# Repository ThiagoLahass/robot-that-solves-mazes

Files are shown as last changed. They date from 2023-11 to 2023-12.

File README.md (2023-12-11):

# robot-that-solves-mazes
Apply concepts acquired throughout the course such as pulse width modulation (PWM) for controlling DC motors and servomotors, analog-to-digital conversion (ADC) for data collection signals from analog sensors, port control (GPIO, General Purpose Input/Output), Timers, LCD, among others.

<div style="display: flex; justify-content: space-between;">
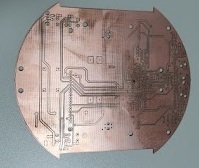
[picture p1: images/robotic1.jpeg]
  
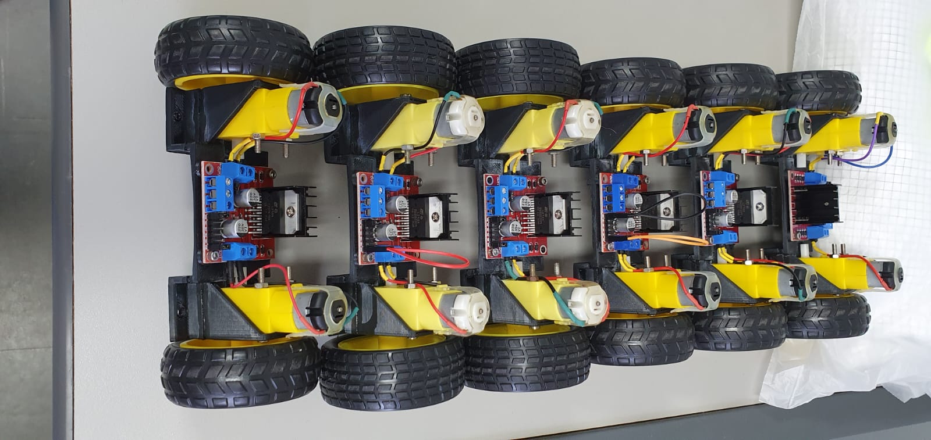
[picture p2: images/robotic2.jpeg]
  
</div>

## Video Demonstration

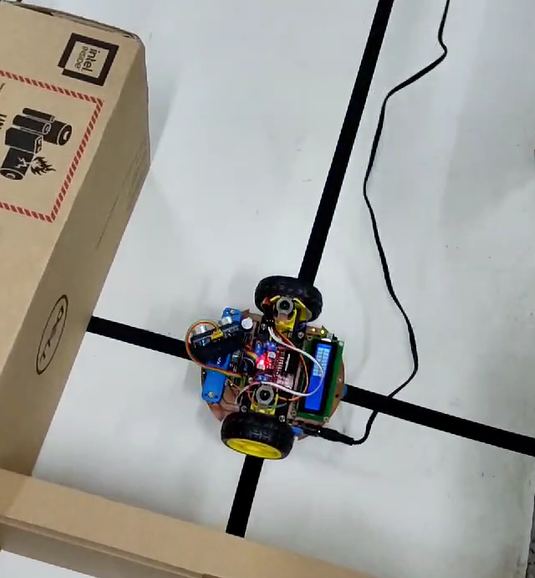
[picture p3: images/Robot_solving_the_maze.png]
Watch the Demo Video (https://youtu.be/FQmdxKDgYJk)


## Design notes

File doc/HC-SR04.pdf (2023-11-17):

## HC-SR04 Ultrasonic Sensor

### Elijah J. Morgan Nov. 16 2014

The purpose of this file is to explain how the HC-SR04 works. It will give a brief explanation of how ultrasonic sensors work in general. It will also explain how to wire the sensor up to a microcontroller and how to take/interpret readings. It will also discuss some sources of errors and bad readings.

### 1. How Ultrasonic Sensors Work 2. HC-SR04 Specifications 3. Timing chart, Pin explanations and Taking

Distance Measurements

### 4. Wiring HC-SR04 with a microcontroller 5. Errors and Bad Readings

### 1. How Ultrasonic Sensors Work

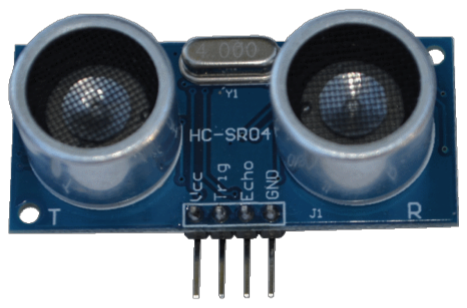
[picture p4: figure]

Ultrasonic sensors use sound to determine the distance between the sensor and the closest object in its path. How do ultrasonic sensors do this? Ultrasonic sensors are essentially sound sensors, but they operate at a frequency above human hearing.

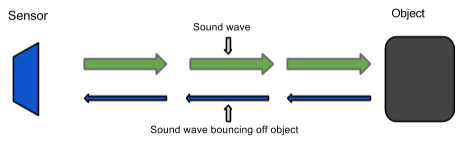
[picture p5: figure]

The sensor sends out a sound wave at a specific frequency. It then listens for that specific sound wave to bounce off of an object and come back (Figure 1). The sensor keeps track of the time between sending the sound wave and the sound wave returning. If you know how fast something is going and how long it is traveling you can find the distance traveled with equation 1.

Equation 1. d = v × t

The speed of sound can be calculated based on the a variety of atmospheric conditions, including temperature, humidity and pressure. Actually calculating the distance will be shown later on in this document.
It should be noted that ultrasonic sensors have a cone of detection, the angle of this cone varies with distance, Figure 2 show this relation. The ability of a sensor to detect an object also depends on the objects orientation to the sensor. If an object doesn’t present a flat surface to the sensor then it is possible the sound wave will bounce off the object in a way that it does not return to the sensor.

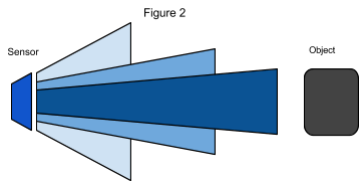
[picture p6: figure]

### 2. HC-SR04 Specifications

The sensor chosen for the Firefighting Drone Project was the HC-SR04. This section contains the specifications and why they are important to the sensor module. The sensor modules requirements are as follows.
- Cost
- Weight
- Community of hobbyists and support
- Accuracy of object detection
- Probability of working in a smoky environment
- Ease of use
The HC-SR04 Specifications are listed below. These specifications are from the Cytron Technologies HC-SR04 User’s Manual (source 1).
- Power Supply: +5V DC
- Quiescent Current: <2mA
- Working current: 15mA
- Effectual Angle: <15º
- Ranging Distance: 2-400 cm
- Resolution: 0.3 cm
- Measuring Angle: 30º
- Trigger Input Pulse width: 10uS
- Dimension: 45mm x 20mm x 15mm
- Weight: approx. 10 g

The HC-SR04’s best selling point is its price; it can be purchased at around $2 per unit.

### 3. Timing Chart and Pin Explanations

The HC-SR04 has four pins, VCC, GND, TRIG and ECHO; these pins all have different functions. The VCC and GND pins are the simplest they power the HC-SR04. These pins need to be attached to a +5 volt source and ground respectively. There is a single control pin: the TRIG pin. The TRIG pin is responsible for sending the ultrasonic burst. This pin should be set to HIGH for 10 μs, at which point the HC-SR04 will send out an eight cycle sonic burst at 40 kHZ. After a sonic burst has been sent the ECHO pin will go HIGH. The ECHO pin is the data pin it is used in taking distance measurements. After an ultrasonic burst is sent the pin will go HIGH, it will stay high until an ultrasonic burst is detected back, at which point it will go LOW.
Taking Distance Measurements
The HC-SR04 can be triggered to send out an ultrasonic burst by setting the TRIG pin to HIGH. Once the burst is sent the ECHO pin will automatically go HIGH. This pin will remain HIGH until the the burst hits the sensor again. You can calculate the distance to the object by keeping track of how long the ECHO pin stays HIGH. The time ECHO stays HIGH is the time the burst spent traveling. Using this measurement in equation 1 along with the speed of sound will yield the distance travelled. A summary of this is listed below, along with a visual representation in Figure 2.
1. Set TRIG to HIGH
2. Set a timer when ECHO goes to HIGH
3. Keep the timer running until ECHO goes to LOW
4. Save that time
5. Use equation 1 to determine the distance travelled

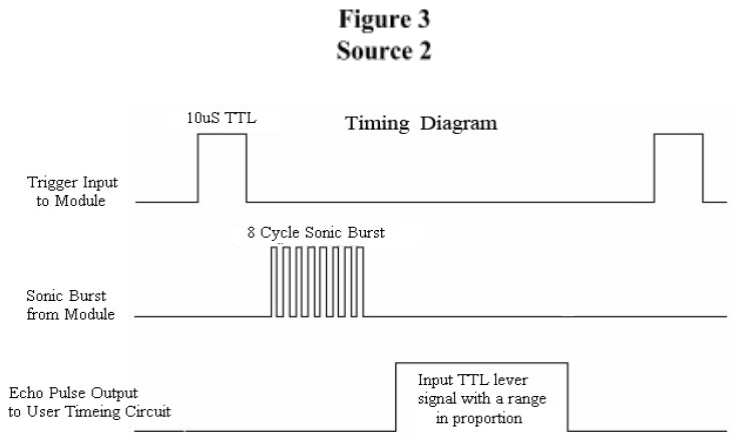
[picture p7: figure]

Source 2

To interpret the time reading into a distance you need to change equation 1. The clock on the device you are using will probably count in microseconds or smaller. To use equation 1 the speed of sound needs to determined,which is 343 meters per second at standard temperature and pressure. To convert this into more useful form use equation 2 to change from meters per second to microseconds per centimeter. Then equation 3 can be used to easily compute the distance in centimeters.

Equation 2. Distance =

Speed
170.15 m × 100 cm

Meters ×

1e6 μS
170.15 m × cm

58.772 μS

Equation 3. Distance = 58 | m

time =

μs
μs/cm = c

### 4. Wiring the HC-SR04 to a Microcontroller

This section only covers the hardware side. For information on how to integrate the software side, look at one of the links below or look into the specific microcontroller you are using.

The HC-SR04 has 4 pins: VCC, GND, TRIG and ECHO.
1. VCC is a 5v power supply. This should come from the microcontroller
2. GND is a ground pin. Attach to ground on the microcontroller.
3. TRIG should be attached to a GPIO pin that can be set to HIGH
4. ECHO is a little more difficult. The HC-SR04 outputs 5v, which could destroy many microcontroller GPIO pins (the maximum allowed voltage varies). In order to step down the voltage use a single resistor or a voltage divider circuit. Once again this depends on the specific microcontroller you are using, you will need to find out its GPIO maximum voltage and make sure you are below that.

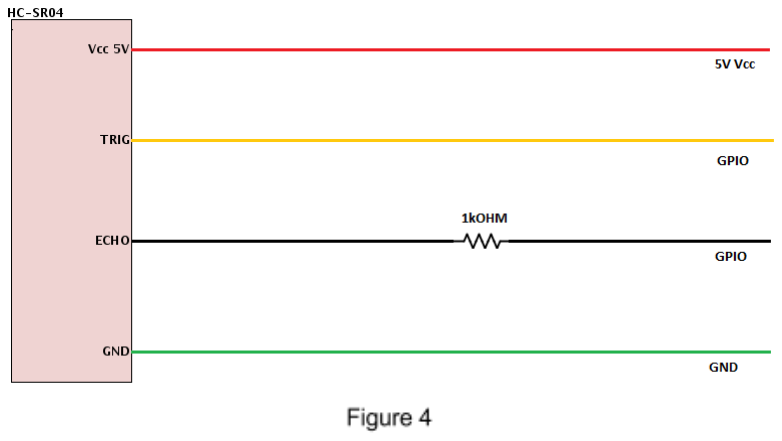
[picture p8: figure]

### 5. Errors and Bad Readings

Ultrasonic sensors are great sensors they work well for many applications where other types of sensors fall short. Unfortunately, they do have weaknesses. These weaknesses can be mitigated and worked around, but first they must be understood. The first weakness is that they use sound. There is a limit to how fast ultrasonic sensors can get distance measurements. The longer the distance, the slower they are at reporting the distance. The second weakness comes from the way sound bounces off of objects. In enclosed spaces it is possible, if not probable that there will be unintended echos. The echos can very easily cause false short readings. In Figure 2 a pulse was sent out. It bounced off of object 1 and returned to the sensor. The distance was recorded and then a new pulse was sent. There was another object farther away, so that when the new pulse reaches object 1, the first signal will reach the sensor. This will cause the sensor to think that there is an object closer than is actually true. The old pulse is smaller than the new pulse because it has grown weaker. The longer the pulse exists the weaker it grows until it is negligible. If multiple sensors are being used, the number of echos will increase along with the number of errors. There are two main ways to reduce the number of errors. The first is to provide shielding around the sensor. This prevents echos coming in from angle outside what the sensor should actually pick up. The second is to reduce the frequency at which pulses are sent out. This gives more time for the echos to dissipate.

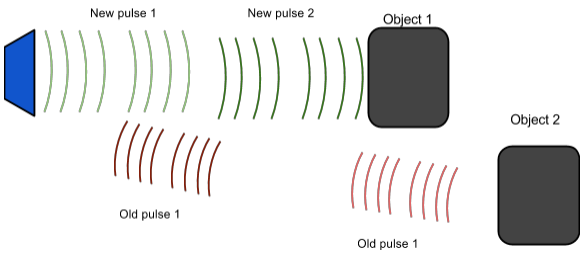
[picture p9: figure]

Works Cited

Source 1.
“HC-SR04 User's_Manual.” docs.google. Cytron Technologies, May 2013 Web. 5 Dec. 2009.
<https://docs.google.com/document/d/1Y-yZnNhMYy7rwhAgyL_pfa39RsB-x2qR4vP8saG73rE/edit>

Source 2.
“Attiny2313 Ultrasonic distance (HR-SR04) example.” CircuitDB. n.a. 7 Sept. 2014 Web. 5 Dec. 2014. <http://www.circuitdb.com/?p=1162>

Links

These are not formatted; you will need to copy and paste them into your web browser.

Want to learn about Ultrasonic Sensors in general? http://www.sensorsmag.com/sensors/acousticultrasound/choosingultrasonicsensorprox imityordistancemeasurement-825

All about the HC-SR04

- http://www.circuitdb.com/?p=1162
- http://www.micropik.com/PDF/HCSR04.pdf
- http://randomnerdtutorials.com/completeguideforultrasonicsensorhcsr04/
- http://www.ezdenki.com/ultrasonic.php
(^fantastic tutorial, explains a lot of stuff)
- http://www.elecrow.com/hcsr04-ultrasonicrangingsensorp-316.html
(^ this one has some cool charts)

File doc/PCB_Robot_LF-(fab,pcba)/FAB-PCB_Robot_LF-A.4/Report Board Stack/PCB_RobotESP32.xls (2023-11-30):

Board Stack Report
Stack Up |  | Layer Stack
Layer | Board Layer Stack | Name | Material | Thickness | Constant
1 |  | Top Paste
2 |  | Top Overlay
3 |  | Top Solder | Solder Resist | 0.40mil | 3.5
4 |  | Top Layer | Copper | 1.40mil
5 |  | Dielectric 1 | FR-4 | 12.60mil | 4.8
6 |  | Bottom Layer | Copper | 1.40mil
7 |  | Bottom Solder | Solder Resist | 0.40mil | 3.5
8 |  | Bottom Overlay
9 |  | Bottom Paste
 | Height : 16.20mil

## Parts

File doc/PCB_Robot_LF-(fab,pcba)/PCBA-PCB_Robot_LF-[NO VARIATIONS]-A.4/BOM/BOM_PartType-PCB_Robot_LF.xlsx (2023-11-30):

Comment | Description | Designator | Footprint | LibRef | Quantity
MPU-6050 | 3-axis gyroscope, 3-axis accelerometer |  | PCBComponent_1 | CMP-1172158-22 | 1
2AA-BH | holder for 2AA Batteries | B1, B2 | PCB-372er05q764edivmfsgk-1 | CMP-3614-18 | 2
2.2 nF | Cap Ceramic 0.1uF 100V X7R 10% SMD 0805 125°C Embossed Plastic T/R | C1, C2, C3, C4, C5 | PCB-uuh55xovs16kiz8jvqzd-1 | CMP-27afecb34382f868-1 | 5
Zener 5V | Zener Diode Single 5.6V | D1 | Vishay TZMB5V6-GS08-Footprint-1 | CMP-0f7fc64f132dd0b8-2 | 1
Taiwan Semiconductor SS14L | Diode: Schottky rectifying; 40V; 1A; subSMA | D2, D5 | SS14L | CMP-32c6fbb69da8ed01-1 | 2
Bivar SM0805GCL | LED; SMD; 0805; Green; 575nm; 3.6mcd; Water Clr Lens; 130Deg Viewing Angle; Low Current | D3, D4 | PCB-iso4q9antg7ukfc6uypa-1 | CMP-5ccb9491e398830c-1 | 2
Custom LCD | Custom LCD | DS* | PCB-a1k1vgfry79p3zq61c6u-1 | CMP-bd58754c3093629f-2 | 1
Molex 10-89-7061 | Conn.; Rect./PCB; Breakaway Header; 6 Cir.; 2-Row; Vert.; C-Grid Series; High Temp; Tin | J1, J2, J3, J4, J5 | PCB-cmxxrm6j1415z55ls37o-1 | CMP-a3b96ab7ba957c7e-1 | 5
Würth Elektronik 694108301002 | DC Power Jack Connector WR-DC, Male, Right Angled, THT, 5 A, 24 V | J6 | PCB-vi56m6hkignhj9lwk7ra-1 | CMP-fe0834211d6821cf-4 | 1
GPS NEO-6M | KK 254 Solid Header, Vertical, with Friction Lock, 4 Circuits, Tin (Sn) Plating | J7 | PCB-hddxo6oxno0y1grizy36-1 | CMP-cef707fdef991130-9 | 1
HC-S04 | KK 254 Solid Header, Vertical, with Friction Lock, 4 Circuits, Tin (Sn) Plating | J8 | PCB-hddxo6oxno0y1grizy36-1 | CMP-cef707fdef991130-9 | 1
MotoresDC | Conn Unshrouded Header HDR 8 POS 2.54mm Solder ST Top Entry Thru-Hole Bag/Box | JP1 | PCB-zdm29xznpx2fif9lk3na-1 | CMP-1d33d663ca37c2f4-5 | 1
150080YS75000 | SMD mono-color Chip LED; WL-SMCW; Yellow | LED1, LED2 | 0805_A | CMP-12518870-5 | 2
MP2307_Buck | MP2307 Buck | Module1 | PCB-8fho96w7wpsiqoq4hq4v-1 | CMP-f3b73942b0d12c70-1 | 1
ServoMotor | AMPMODU 3 Position Through-Hole Single Row 0.1 Inch Straight Breakaway Header | P1 | PCB-t3j82fujp56a0y7cbkwq-1 | CMP-56249debc17089e3-37 | 1
TRCT5000_3 | Optical Switches, Reflective, Phototransistor Output 12mm Sense 950nm | Q1 | PCB-TCRT5000 | CMP-udi2hivl2amq5tnk7plz-1 | 1
TRCT5000 | Optical Switches, Reflective, Phototransistor Output 12mm Sense 950nm | Q2, Q3, Q4, Q5 | PCB-TCRT5000 | CMP-udi2hivl2amq5tnk7plz-1 | 4
MMBTH10LT1G | VHF / UHF Transistor, NPN Silicon, 3-Pin SOT-23, Pb-Free, Tape and Reel | Q6, Q7, Q8, Q9, Q10 | ONSC-SOT-23-3-318-08_V | CMP-851888-2 | 5
220 | Res Thick Film 0805 330 Ohm 1% 1/8W ±100ppm/°C Molded SMD SMD | R1, R2, R19, R20, R21, R22, R23 | CAPC2013X94X50ML20T25 | CMP-d14418bba6eb0e83-1 | 7
330 | Res Thick Film 0805 330 Ohm 1% 1/8W ±100ppm/°C Molded SMD SMD | R3, R4, R5, R6, R7, R8, R9, R10, R11, R18, R24, R25 | CAPC2013X94X50ML20T25 | CMP-d14418bba6eb0e83-1 | 12
1 k | Res Thick Film 0805 330 Ohm 1% 1/8W ±100ppm/°C Molded SMD SMD | R12, R13, R14, R15, R26, R27, R28, R29, R30, R33 | CAPC2013X94X50ML20T25 | CMP-d14418bba6eb0e83-1 | 10
4k7 | Res Thick Film 0805 330 Ohm 1% 1/8W ±100ppm/°C Molded SMD SMD | R16 | CAPC2013X94X50ML20T25 | CMP-d14418bba6eb0e83-1 | 1
3k7 | Res Thick Film 0805 330 Ohm 1% 1/8W ±100ppm/°C Molded SMD SMD | R17 | CAPC2013X94X50ML20T25 | CMP-d14418bba6eb0e83-1 | 1
2 k | Res Thick Film 0805 330 Ohm 1% 1/8W ±100ppm/°C Molded SMD SMD | R31 | CAPC2013X94X50ML20T25 | CMP-d14418bba6eb0e83-1 | 1
47 k | Res Thick Film 0805 330 Ohm 1% 1/8W ±100ppm/°C Molded SMD SMD | R32 | CAPC2013X94X50ML20T25 | CMP-d14418bba6eb0e83-1 | 1
SPI | Conn Unshrouded Header HDR 6 POS 2.54mm Solder ST Thru-Hole - No Outline | SPI | PCB-2xrknp0frdgvb29ud8aa-1 | CMP-88ed4362af17572a-9 | 1
C&K Components OS102011MA1QS1 | Switch Slide ON ON SPDT Side Slide 0.1A 12VDC 10000Cycle PC Pins Bracket Mount/Through Hole Bulk | SW1 | PCB-a78kgj8v3nza1899t3lg-1 | CMP-85734c5fa66e5ab4-3 | 1
TE Connectivity 1825910-6 | Switch Push Button OFF (ON) SPST Round Button 0.05A 24VDC Momentary Contact PC Pins Thru-Hole | SW2, SW3, SW4, SW5 | PCB-s0s7ww4bjhs8rpuf9xpk-1 | CMP-49fa8280b69c963d-7 | 4
MT3608 Module | MT3608 Module DC - DC Boost | U | MT3608-Module | CMP-da4e14b3e5cd0589-10 | 1
ESP32 Custom | Eval Board For ESP-WROOM-32 - 38pin module with 8.4mm header | U2 | PCB-v7o6mlcnvy9ltvisia1k-2 | CMP-0991c5192c5ed656-43 | 1
Trimmer 1/2W | Res Cermet Trimmer 2K Ohm 10% 1/2W 25(Elec)Turn 2.19mm (9.53 X 4.83 X 11.55mm) Pin Thru-Hole Tube | VR1 | PCB-5abvnr99iwiiosfurk6j-1 | CMP-a8df61d7bf077718-3 | 1
OBO 1206A | Audio Buzzer Piezo 85dB | X1 | PCB-o5yglm5fvhcnnvl903n6-1 | CMP-hk97o7c7kcbk1p7rfoz4-1 | 1

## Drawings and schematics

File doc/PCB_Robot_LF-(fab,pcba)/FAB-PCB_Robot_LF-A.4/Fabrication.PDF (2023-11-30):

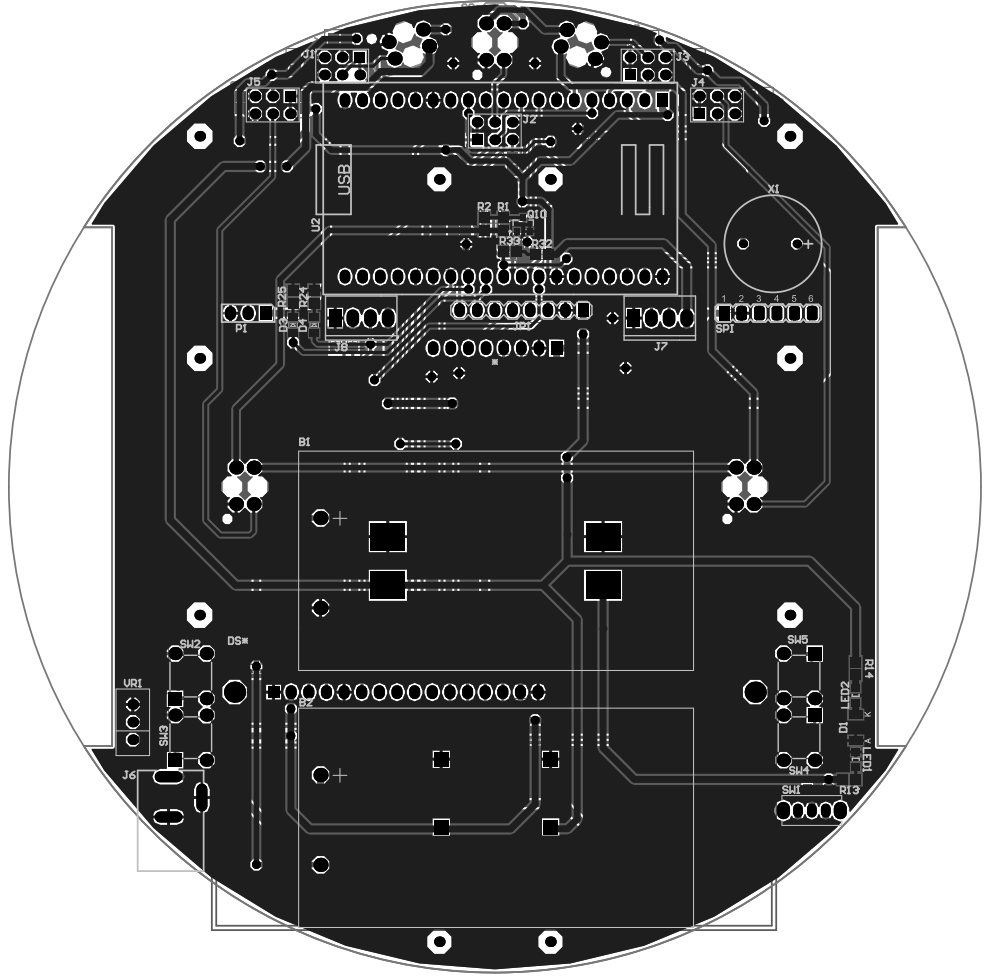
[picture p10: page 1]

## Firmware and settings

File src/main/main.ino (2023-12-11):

#include <ESP32Servo.h>
#include "Wire.h"
#include <MPU6050_light.h>
#include <string.h>

#define     HIGH        1
#define     LOW         0

//=== NAMING THE PORTS ===
#define     SLC         32
#define     SR          39
#define     SC          34
#define     SL          35
#define     SRC         36
#define     E_CH1       33
#define     CHA_M1      25
#define     E_CH2       26
#define     CHA_M2      27
#define     BUZZER      14
#define     BL_LCD      12
#define     SERVO       13
#define     DB4         15
#define     DB5         2
#define     DB6         0
#define     DB7         4
#define     EN_TRIG     16
#define     RS          17
#define     CS_SENSORS  5
#define     CLK         18
#define     MISO_ECHO   19
#define     SDA_MPU     21
#define     RX0         3
#define     TX0         1
#define     SCL_MPU     22
#define     MOSI        23
//=========================

//============================= LCD COMMANDS =============================
const int DATA[] = {4, 0, 2, 15};
#define     DATA_SIZE 4

// Commands: [- - - RS D7 D6 D5 D4]
#define     FUNCTION_SET 	      0x20 	// 0010 0000 - 4 bits
#define     DISPLAY_CONTROL     0x0C 	// 0000 1100
#define     CLEAR_DISPLAY 	    0x01 	// 0000 0001
#define     RETURN_HOME 	      0x02 	// 0000 0010
#define     ENTRY_MODE_SET 	    0x06 	// 0000 0110

// States
#define     LCD_DISPLAYON 		  0x04
#define     LCD_DISPLAYOFF 		  0x00
#define     DISPLAY_FUNCTION 	  0x08
#define     ENTER 				      0xA8  //1010 1000
#define     DISPLAY_SHIFT_LEFT 	0x18  //0001 1000
#define     DISPLAY_SHIFT_RIGHT 0x1C  //0001 1100

void pulseEnable();
void initLCD();
void write4bits(int value);
void write8bits(int value);

void writeData(const char* value){
  char c;
  for (int i = 0; i < strlen(value); i++){
    c = value[i];
    
    digitalWrite(RS, HIGH);
    write8bits(c);
    digitalWrite(RS, LOW);
  }
}

void display_sensors_values_on_LCD();
// ============================= END LCD COMMANDS =============================

// Private Objects and Variables for giroscope
MPU6050 mpu(Wire);
unsigned long timer = 0;

// DEFINES OF VALUES RELATED TO ENGINE CONTROL
#define     PWM1_Ch     2       // Direita
#define     PWM2_Ch     3       // Esquerda
#define     PWM_Res     8
#define     PWM_Freq    1000

#define     LINE_THRESHOLD_VALUE 500      // line reading cut-off value
#define     WALL_THRESHOLD_VALUE 30       // wall reading cut-off value
#define     ANGLE_TURN_VALUE 83           // angle that robot must turn based on giroscope value
#define     TIME_TO_RESTART 15            // seconds
#define     NUM_SENSORS 5

unsigned int sensors[NUM_SENSORS]       = {0};      // an array to hold sensor values
unsigned int sensors_max[NUM_SENSORS]   = {0};      // used to calibrate the initial values of the IR sensors
unsigned int sensors_min[NUM_SENSORS]   = {4096};   // used to calibrate the initial values of the IR sensors

float Kp = 0.008, Ki = 0, Kd = 0;                   // values of the PID constants values

char path[100] = "";

unsigned char path_length = 0;                      // the length of the path


float moving_average(float *buffer, int tamanho);

float read_ultrasonic_sensor();

void follow_segment();

void turn_off_motors();

void read_line();

void turn(char dir);

char select_turn(unsigned char found_left, unsigned char found_straight, unsigned char found_right);

void simplify_path();

void set_motors(int right_motor, int left_motor);

void lcd_load_custom_character();

const int SIZE_MOVING_AVERAGE = 5;
float buffer[SIZE_MOVING_AVERAGE] = {0};

Servo servo;                        // create servo object to control a servo
int pos = 0;                        // variable to store the servo position

float average_distance = 0;         // average distance read by the ultrasonic sensor

void setup() {
  Serial.begin(115200);
  Wire.begin();
  byte status = mpu.begin();
  while(status != 0){ }             // stop everything if could not connect to MPU6050
  delay(500);
  mpu.calcOffsets();                // gyro and accelero

  pinMode(EN_TRIG, OUTPUT);
  pinMode(MISO_ECHO, INPUT);

  pinMode(BUZZER, OUTPUT);
  digitalWrite(BUZZER, LOW);

  servo.attach(SERVO, 500, 2500);   // attaches the servo on pin SERVO to the servo object
  servo.write(90);                  // Position the servo in the central position
  delay(500);

  pinMode(SLC       , INPUT);
  pinMode(SR        , INPUT);
  pinMode(SC        , INPUT);
  pinMode(SL        , INPUT); 
  pinMode(SRC       , INPUT);
  pinMode(CS_SENSORS, OUTPUT);

  digitalWrite(CS_SENSORS, HIGH);

  pinMode(E_CH1, OUTPUT);
  pinMode(E_CH2, OUTPUT);

  ledcAttachPin(CHA_M1, PWM1_Ch);
  ledcSetup(PWM1_Ch, PWM_Freq, PWM_Res);

  ledcAttachPin(CHA_M2, PWM2_Ch);
  ledcSetup(PWM2_Ch, PWM_Freq, PWM_Res);

  // ========================== LCD ==========================
  pinMode(RS, OUTPUT);
  pinMode(EN_TRIG, OUTPUT);
  
  for (int i = 0; i < DATA_SIZE; i++){
    pinMode(DATA[i], OUTPUT);
  }

  initLCD();
  
  // Always good to clear and return home
  write8bits(CLEAR_DISPLAY);
  write8bits(RETURN_HOME);
  delay(2);                         // 1.52ms delay needed for the Return Home command

  writeData("Thiago Lahass");
  write8bits(ENTER);
  writeData("Eng Computacao");
}
    
void loop() {
  //======================== APPLYING LEARNING ALGORITHM ========================
  while(1){
    delay(100);

    follow_segment();

    read_line();
    // If we no longer find a visible line, we finish the maze and can restart from the optimized path
    if(sensors[1] < LINE_THRESHOLD_VALUE && sensors[2] < LINE_THRESHOLD_VALUE && sensors[3] < LINE_THRESHOLD_VALUE ){
      Serial.println("No lines found, DONE!!!");
      break;
    }

    // set the motors bit more slowly
    set_motors(158, 94); // (128 + 30, 128 - 34) - apparently the motor on the right runs a little more with the same pwm than the one on the left, hence the difference
    read_line();

    // If the crossing sensors are already on the line, leave immediately
    // if not, walk a little further until you find the crossing line.
    while(sensors[0] < LINE_THRESHOLD_VALUE && sensors[4] < LINE_THRESHOLD_VALUE){
      read_line();
    }

    // stop the motors
    turn_off_motors();
    delay(100);

    //================== FOLLOWING THE MAZE ACCORDING TO THE WALLS ==================
    //================================ READ THE WALLS ===============================
    unsigned char found_left      = 0;
    unsigned char found_straight  = 0;
    unsigned char found_right     = 0;

    servo.write(90);                                    // Servo facing forward
    delay(500);
    average_distance = read_ultrasonic_sensor();
    display_sensors_values_on_LCD();
    
    if(average_distance > WALL_THRESHOLD_VALUE){
      found_straight = 1;
      Serial.println("found_straight");
    }

    servo.write(180);                                   // Servo facing left
    delay(500);
    average_distance = read_ultrasonic_sensor();
    display_sensors_values_on_LCD();

    if( average_distance > WALL_THRESHOLD_VALUE ){      // If the left is free, we can take it immediately
      found_left = 1;
      Serial.println("found_left");
    } 
    else{
      servo.write(0);                                   // Servo facing right
      delay(500);
      average_distance = read_ultrasonic_sensor();
      display_sensors_values_on_LCD();

      if(average_distance > WALL_THRESHOLD_VALUE){
        found_right = 1;
        Serial.println("found_right");
      }
    }

    servo.write(90);                                    // Servo facing forward
    //============================ END OF THE READ WALLS SECTION ==============================

    // Intersection identification is complete.

    unsigned char dir = select_turn(found_left, found_straight, found_right);
    Serial.print("Direção: ");
    Serial.println((char)dir);
    
    // Make the turn indicated by the path.
    turn(dir);
    
    // Store the intersection in the path variable.
    path[path_length] = dir;
    path_length ++;

    Serial.print("Path: ");
    Serial.println(path);

    // simplify the path
    simplify_path();
    Serial.print("Simplified Path: ");
    Serial.println(path);
  }
  
  // Now enter an infinite loop - we can re-run the maze as many times as we want to.
  while(1) {
    // Always good to clear and return home
    write8bits(CLEAR_DISPLAY);
    write8bits(RETURN_HOME);
    delay(2);                               // 1.52ms delay needed for the Return Home command

    writeData("DONE!!!");
    write8bits(ENTER);
    writeData("Restart please...");
    delay(1000);

    
    // Always good to clear and return home
    write8bits(CLEAR_DISPLAY);
    write8bits(RETURN_HOME);
    delay(2);                               // 1.52ms delay needed for the Return Home command
    writeData("Restarting in...");
    
    int j = 0;
    for(j = 0; j < TIME_TO_RESTART; j++) {
      
      char line[25];
      line[0] = '\0';
      dtostrf(j, 6, 2, line);
      strcat(line, " s");

      // writeData("Restarting in...");
      write8bits(ENTER);
      writeData(line);
      delay(1000);
    }

    int i;
    for(i = 0; i < path_length; i++) {
      // SECOND MAIN LOOP BODY
      follow_segment();
      
      // Drive straight while slowing down, as before.
      set_motors(158, 94);  // (128 + 30, 128 - 34) - apparently the motor on the right runs a little more with the same pwm than the one on the left, hence the difference
      read_line();

      // If the crossing sensors are already on the line, leave immediately
      // if not, walk a little further until you find the crossing line.
      while(sensors[0] < LINE_THRESHOLD_VALUE && sensors[4] < LINE_THRESHOLD_VALUE){
        read_line();
      }

      // stop the motors
      turn_off_motors();
      delay(100);
    
      // Make a turn according to the instruction stored in
      // path[i].
      turn(path[i]);
    }
    // Follow the last segment up to the finish.
    follow_segment();
    
    // Now we should be at the finish! Restart the loop.
  }
}

// Function to calculate the moving average
float moving_average(float *buffer, int size) {
    float sum = 0.0;
    for (int i = 0; i < size; ++i) {
        sum += buffer[i];
    }
    return sum / size;
}

// Function to obtain reading from the ultrasonic sensor
float read_ultrasonic_sensor() {
    float duration, distance;
    for(int i = 0; i < SIZE_MOVING_AVERAGE; i++){
        // Send a short pulse to the Trig pin to activate measurement
        digitalWrite(EN_TRIG, LOW);
        delayMicroseconds(10);
        digitalWrite(EN_TRIG, HIGH);
        delayMicroseconds(10);
        digitalWrite(EN_TRIG, LOW);

        // Measure pulse duration on Echo pin
        duration = pulseIn(MISO_ECHO, HIGH);

        // Convert duration to distance (considering speed of sound ~343m/s)
        distance = duration * 0.0343 / 2;

        buffer[i] = distance;
    }

    // Calculation of the moving average
    float average_distance = moving_average(buffer, SIZE_MOVING_AVERAGE);

    return average_distance;
}


// FOLLOWING A SEGMENT USING ON-OFF CONTROL (not used here, for testing only)
void follow_segment_on_off() {
    while(1) {
        read_line();

        if( sensors[1] > LINE_THRESHOLD_VALUE ){        // must rotate to right
          set_motors(128+42, 128-22);
        }
        else if( sensors[3] > LINE_THRESHOLD_VALUE ){   // must rotate to left
          set_motors(128+22, 128-42);
        }
        else if( sensors[2] > LINE_THRESHOLD_VALUE  ){
          set_motors(128+42, 128-42);
        }
        else{
          set_motors(128, 128);
        }
    }
}


// FOLLOWING A SEGMENT USING PID CONTROL
void follow_segment() {
    int     last_proportional_left   = 0;
    long    integral_left            = 0;

    int     last_proportional_right  = 0;
    long    integral_right           = 0;

    unsigned long initial_time, atual_time;
    initial_time = millis();

    while(1) {
        read_line();

        // The "proportional" term should be 0 when we are on the line.
        float proportional_left  = sensors[1];
        float proportional_right = sensors[3];

        // Compute the left derivative (change) and integral (sum) of the position.
        int derivative_left = proportional_left - last_proportional_left;
        integral_left += proportional_left;

        // Compute the right derivative (change) and integral (sum) of the position.
        int derivative_right = proportional_right - last_proportional_right;
        integral_right += proportional_right;

        // Remember the last position.
        last_proportional_left = proportional_left;
        last_proportional_right = proportional_right;

        // Compute the difference between the two motor power settings,
        // m1 - m2. If this is a positive number the robot will turn
        // to the left. If it is a negative number, the robot will
        // turn to the right, and the magnitude of the number determines
        // the sharpness of the turn.
        int power_difference_left  = proportional_left*Kp + integral_left*Ki + derivative_left*Kd;
        int power_difference_right = proportional_right*Kp + integral_right*Ki + derivative_right*Kd;

        set_motors(167 + power_difference_left, 85 - power_difference_right); // direita, esquerda

        // We use the inner three sensors (1, 2, and 3) for
        // determining whether there is a line straight ahead, and the
        // sensors 0 and 4 for detecting lines going to the left and
        // right.
        atual_time = millis();

        if( atual_time > initial_time + 1000){
            if(sensors[1] > LINE_THRESHOLD_VALUE && sensors[2] > LINE_THRESHOLD_VALUE && sensors[3] > LINE_THRESHOLD_VALUE ) {
              // There is no line visible ahead, and we didn't see any
              // intersection. Must be a dead end.
              Serial.println("Intersection 3 lines found");
              return;
            }
            else if(sensors[0] > LINE_THRESHOLD_VALUE || sensors[4] > LINE_THRESHOLD_VALUE){
                // Found an intersection.
                if( sensors[0] > LINE_THRESHOLD_VALUE ){
                    Serial.println("Intersection left found");
                }
                if( sensors[0] > LINE_THRESHOLD_VALUE ){
                    Serial.println("Intersection right found");
                }
                return;
            }
            else if(sensors[1] < LINE_THRESHOLD_VALUE && sensors[2] < LINE_THRESHOLD_VALUE && sensors[3] < LINE_THRESHOLD_VALUE ){
              Serial.println("No lines found, DONE!!!");
              turn_off_motors();
              return;
            }
        }
    }
}


void set_motors(int right_motor, int left_motor){
    digitalWrite(E_CH1, HIGH);
    digitalWrite(E_CH2, HIGH);
    ledcWrite(PWM1_Ch, right_motor);  // Right motor channel CHA_M1
    ledcWrite(PWM2_Ch, left_motor);   // Left  motor channel CHA_M2
    return;
}

void turn_off_motors(){
    digitalWrite(E_CH1, LOW);
    digitalWrite(E_CH2, LOW);
    return;
}

// Turns according to the parameter dir, which should be 'L', 'R', 'S' (straight), or 'B' (back).
void turn (char dir) {
  mpu.update();
  float initial_position = mpu.getAngleZ();
  float current_position = initial_position;

  Serial.print("initial_position: ");
  Serial.println(initial_position);

    switch(dir) {
        case 'L':
            // Turn left with giroscope
            Serial.println("Esquerda");
            set_motors(128+45, 128+45);
            while( current_position < initial_position + ANGLE_TURN_VALUE ){
              mpu.update();
              current_position = mpu.getAngleZ();
              // Serial.println(current_position);
            }

            turn_off_motors();
            break;

            // Turn left with infra-red line sensors
            // set_motors(128+35, 128+35);
            // Serial.println(mpu.getAngleZ());
            // while( sensors[2] > LINE_THRESHOLD_VALUE ){
            //   read_line();
            // }
            // while(sensors[2] < LINE_THRESHOLD_VALUE){
            //   read_line();
            // }
            // set_motors(128, 128);
            // break;

        case 'R':
            // Turn right with giroscope
            Serial.println("Direita");
            set_motors(128-45, 128-45);
            while( current_position > initial_position - ANGLE_TURN_VALUE ){
              mpu.update();
              current_position = mpu.getAngleZ();
              Serial.print("current_position: ");
              Serial.println(current_position);
            }

            turn_off_motors();
            break;

            // // Turn right with line sensors
            // set_motors(128-35, 128-35);
            // while( sensors[2] > LINE_THRESHOLD_VALUE ){
            //   read_line();
            // }
            // while(sensors[2] < LINE_THRESHOLD_VALUE){
            //   read_line();
            // }
            // set_motors(128, 128);
            // break;
        case 'B':
          // Turn around with giroscope
            Serial.println("Back");
            set_motors(128+45, 128+45);
            while( current_position < initial_position + 2 * ANGLE_TURN_VALUE + 5 ){
              mpu.update();
              current_position = mpu.getAngleZ();
              // Serial.println(current_position);
            }

            turn_off_motors();
            break;

            // // Turn around.
            // set_motors(128+35, 128+35);
            // while( sensors[2] > LINE_THRESHOLD_VALUE ){
            //   read_line();
            // }
            // while(sensors[2] < LINE_THRESHOLD_VALUE){
            //   read_line();
            // }
            // set_motors(128, 128);
            // break;
        case 'S':
            // Don't do anything!
            Serial.println("Straight");
            break;
    }
}

// ================= "left hand on the wall" strategy =================
// This function decides which way to turn during the learning phase of
// maze solving. It uses the variables found_left, found_straight, and
// found_right, which indicate whether there is an exit in each of the
// three directions, applying the "left hand on the wall" strategy.
char select_turn(unsigned char found_left, unsigned char found_straight, unsigned char found_right) {
    // Make a decision about how to turn. The following code
    // implements a left-hand-on-the-wall strategy, where we always
    // turn as far to the left as possible.
    if      (found_left)        return 'L';
    else if (found_straight)    return 'S';
    else if (found_right)       return 'R';
    else                        return 'B';
}


// Path simplification. The strategy is that whenever we encounter a
// sequence xBx, we can simplify it by cutting out the dead end. For
// example, LBL -> S, because a single S bypasses the dead end
// represented by LBL.
void simplify_path() {
    // only simplify the path if the second-to-last turn was a 'B'
    if(path_length < 3 || path[path_length-2] != 'B') return;
    
    int total_angle = 0;
    int i;
    
    for( i = 1; i <= 3; i++) {
        switch( path[path_length - i] ) {
            case 'R':
                total_angle += 90;
                break;
            case 'L':
                total_angle += 270;
                break;
            case 'B':
                total_angle += 180;
                break;
        }
    }

    // Get the angle as a number between 0 and 360 degrees.
    total_angle = total_angle % 360;

    // Replace all of those turns with a single one.
    switch(total_angle) {
        case 0:
            path[path_length - 3] = 'S';
            break;
        case 90:
            path[path_length - 3] = 'R';
            break;
        case 180:
            path[path_length - 3] = 'B';
            break;
        case 270:
            path[path_length - 3] = 'L';
            break;
    }

    // The path is now two steps shorter.
    path_length -= 2;
}


// This takes a sensor reading and returns an estimate of
// the robot’s position with respect to the line, as a number between 0 and 4000. A value of
// 0 means that the line is to the left of sensor 0, value of 1000 means that the line is directly
// under sensor 1, 2000 means that the line is directly under sensor 2, and so on.

// Here is a simplified version of the code that reads the sensors

// Through experiments, the values vary between:
// 100% WHITE =~ 0
// 100% BLACK =~ 2700
void read_line(){
  sensors[0] = analogRead(SLC);
  sensors[1] = analogRead(SL);
  sensors[2] = analogRead(SC);
  sensors[3] = analogRead(SR);
  sensors[4] = analogRead(SRC);

  // Serial.print(sensors[0]);
  // Serial.print(" ");

  // Serial.print(sensors[1]);
  // Serial.print(" ");

  // Serial.print(sensors[2]);
  // Serial.print(" ");

  // Serial.print(sensors[3]);
  // Serial.print(" ");

  // Serial.println(sensors[4]);
}

// ============================= LCD COMMANDS =============================
/* ------------------------------------------------------
	Pulses the Enable pin to send data to the display
*/
void pulseEnable(){
  // Making sure the pin is LOW at first
  digitalWrite(EN_TRIG, LOW);
  delayMicroseconds(1);
  
  // Pulse the Enable pin
  digitalWrite(EN_TRIG, HIGH);
  delayMicroseconds(1);
  digitalWrite(EN_TRIG, LOW);
  delayMicroseconds(100);
}
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

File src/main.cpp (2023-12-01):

#include <Servo.h>

#define HIGH 1
#define LOW  0

#define NUM_SENSORS 5

//=== NOMEANDO AS PORTAS ===
//#define   VCC_3_3     1
//#define   EN          2
#define     SLC         36
#define     SR          39
#define     SC          34
#define     SL          35
#define     SRC         32
#define     E_CH1       33
#define     CHA_M1      25
#define     E_CH2       26
#define     CHA_M2      27
#define     BUZZER      14
#define     BL_LCD      12
//#define   GND         14
#define     SERVO       13
//#define   SD2         16
//#define   SD3         17
//#define   CMD         18
//#define   VCC_5       19
//#define   CLK         20
//#define   SD0         21
//#define   SD1         22
#define     DB4         15
#define     DB5         2
#define     DB6         0
#define     DB7         4
#define     EN_TRIG     16
#define     RS          17
#define     CS_SENSORS  5
#define     CLK         18
#define     MISO_ECHO   19
//#define   GND         32
#define     SDA_MPU     21
#define     RX0         3
#define     TX0         1
#define     SCL_MPU     22
#define     MOSI        23
//#define   GND         38
//=========================

#define PWM1_Ch    0
#define PWM2_Ch    1
#define PWM1_Res   8
#define PWM1_Freq  1000



// The set_motors() function in the Pololu AVR Library (see Section 6 for more information) lets you
// set the duty cycle, and it uses 8-bit precision: a value of 255 corresponds to 100% duty cycle. For
// example, to get 67% on M1 and 33% on M2, you would call

// set_motors(171,84);

// To get a slowly decreasing PWM sequence like the one shown in the graph, you would need to write
// a loop that gradually decreases the motor speed over time.


unsigned int sensors[NUM_SENSORS]       = {0};      // an array to hold sensor values
unsigned int sensors_max[NUM_SENSORS]   = {1023};   // used to calibrate the initial values of the IR sensors
unsigned int sensors_min[NUM_SENSORS]   = {0};      // used to calibrate the initial values of the IR sensors

float Kp = 1/20, Ki = 0, Kd = 3/2; // values of the PID constants values


char path[100] = "";

unsigned char path_length = 0; // the length of the path


float mediaMovel(float *buffer, int tamanho);

float lerSensorUltrasonico();

void follow_segment();

void read_line();

void turn (char dir);

char select_turn(unsigned char found_left, unsigned char found_straight, unsigned char found_right);

void simplify_path();

// os valores de right_motor e left_motor devem ser os valores de duty-cycles deles
// exemplos:
// max velocidade: (100, 100)
// parado: (50, 50)
void set_motors(int right_motor, int left_motor);

unsigned int read_battery_millivolts();

void calibrate_line_sensors();

void mapping_sensors_values_to_calibrated_values();

void initialize();

void lcd_load_custom_character();

void print_character();

bool button_is_pressed();

void display_path();



const int TAMANHO_MEDIA_MOVEL = 5;
float buffer[TAMANHO_MEDIA_MOVEL] = {0};

int posicao_servo = 0;	
int direcao_atual = 0;	// 0 indica anti-horario
const int VEL_SERVO = 15; 
Servo servo;

void setup() {
    Serial.begin(9600);
    // pinMode(EN_TRIG, OUTPUT);
    // pinMode(MISO_ECHO, INPUT);

    // servo.attach(SERVO, 500, 2500);
  	// // posiciona o servo na posicao central
    // while( posicao_servo < 90 ){
    //   posicao_servo += VEL_SERVO;
    //   servo.write(posicao_servo);
    //   delay(100);
    // }

    pinMode(SLC   , INPUT);
    pinMode(SR    , INPUT);
    pinMode(SC    , INPUT);
    pinMode(SL    , INPUT); 
    pinMode(SRC   , INPUT);
    pinMode(CS_SENSORS, OUTPUT);

    digitalWrite(CS_SENSORS, HIGH);

    pinMode(E_CH1, OUTPUT);
    pinMode(E_CH2, OUTPUT);
    digitalWrite(E_CH1, HIGH);
    digitalWrite(E_CH2, HIGH);

    ledcAttachPin(CHA_M1, PWM1_Ch);
    ledcSetup(PWM1_Ch, PWM1_Freq, PWM1_Res);

    ledcAttachPin(CHA_M2, PWM2_Ch);
    ledcSetup(PWM2_Ch, PWM1_Freq, PWM1_Res);
}
    
void loop() {

  follow_segment();


    // //============ LEITURA E ATUALIZAÇÃO DA DISTANCIA DO ULTRASOM ==============
    // // Leitura do sensor ultrassônico
    // // Atualização do buffer para média móvel
    // for (int i = TAMANHO_MEDIA_MOVEL - 1; i > 0; --i) {
    //   buffer[i] = buffer[i - 1];
    // }
    // buffer[0] = lerSensorUltrasonico();

    // // Cálculo da média móvel
    // float media = mediaMovel(buffer, TAMANHO_MEDIA_MOVEL);

    // // Impressão da distância
    // Serial.print("Distancia: ");
    // Serial.println(media);

    // //========== FIM LEITURA E ATUALIZAÇÃO DA DISTANCIA DO ULTRASOM ============


    // //========== UPDATE POSICAO SERVO ==========
    // // anti-horario
    // if( direcao_atual == 0 ){
    //   if(posicao_servo >= 180){
    //       direcao_atual = 1;
    //   }
    //   else{
    //       posicao_servo += VEL_SERVO; 
    //   }
    // }
    // else{ //horario
    //   if(posicao_servo <= 0){
    //       direcao_atual = 0;
    //   }
    //   else{
    //       posicao_servo -= VEL_SERVO; 
    //   }
    // }
  
  	// servo.write(posicao_servo);
  
  	// // Impressão da posicao
    // Serial.print("Posicao: ");
    // Serial.println(posicao_servo);

    // //========== FIM UPDATE POSICAO SERVO ==========


    // // read the sensor:
    // read_line();
    // //calibrate the values
    // calibrate_line_sensors();

    // // AQUI TEMOS OS VALORES JÁ CALIBRADOS


    // delay(100);  // Aguarda 0.1 segundo        

    // while(1) {
    //     // FIRST MAIN LOOP BODY
    //     // (when we find the goal, we use break; to get out of this)
        
    //     follow_segment();
        
    //     // Drive straight a bit. This helps us in case we entered the intersection at an angle.
    //     // Note that we are slowing down - this prevents the robot from tipping forward too much.
    //     set_motors(50,50);
    //     delay(50);

    //     // These variables record whether the robot has seen a line to the
    //     // left, straight ahead, and right, whil examining the current intersection.
    //     unsigned char found_left        = 0;
    //     unsigned char found_straight    = 0;
    //     unsigned char found_right       = 0;

    //     unsigned int sensors[5];

    //     // Now read the sensors and check the intersection type.        
    //     read_line(sensors);

    //     // Check for left and right exits.
    //     if(sensors[0] > 100) found_left  = 1;
    //     if(sensors[4] > 100) found_right = 1;

    //     // Drive straight a bit more - this is enough to line up our wheels with the intersection.
    //     set_motors(40,40);
    //     delay(200);

    //     // Check for a straight exit.
    //     read_line(sensors);

    //     if(sensors[1] > 200 || sensors[2] > 200 || sensors[3] > 200) found_straight = 1;

    //     // Check for the ending spot.
    //     // If all three middle sensors are on dark black, we have
    //     // solved the maze.
    //     if(sensors[1] > 600 && sensors[2] > 600 && sensors[3] > 600) break;
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

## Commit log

2023-11-21 :construction: Add the robot schematic
2023-11-21 :construction: Naming the ports following the schematic
2023-11-21 :construction: Updating ultrasonic read function
2023-11-22 :construction: Creating servo configuration and IR sensors calibration function
2023-11-30 :construction: Add schematic files
    [BOM_PartType-PCB_Robot_LF.xlsx, PCB_RobotESP32.xls, Pick Place for PCB_RobotESP32.csv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]
2023-12-07 :construction: Selection the corret way based on the lvisible lines and making the Servo turn
